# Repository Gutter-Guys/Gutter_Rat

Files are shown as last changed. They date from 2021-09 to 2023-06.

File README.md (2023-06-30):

# THIS IS A WIP USE AT YOUR OWN RISK

# Gutter_Rat
Gantry mod for the ender 6

Currently there are two options available - GR6 and GR9. 

It is recommended to look at GR9 as your first option as it is the simpliest upgrade path from a stock Ender 6. GR6 is only for those that wish to run a 6mm belt setup to possibly use the VZBot style of EVA tool heads. Definitely for those more experienced in modifying or customising printers.

The GR9 version is designed to be built with as much of the stock system as possible. Belts, Pulleys, Spacers, Motherboard and Steppers can all be reused or upgraded if you wish. This flexibilty makes this a cheap upgrade to gain access to the brilliant EVA tool head system. 

## Please join us at our Discord server for updates and assistance with the installation!
[Click Me](https://discord.gg/Wgcgkdk7qW)

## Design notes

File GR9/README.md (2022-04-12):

# Gutter_Rat 9mm Variant

This is the original modification. This mod is designed around 9mm belts with toothed GT2 pulleys and new steppers for X/Y, plus a new control board, however is designed to be the least destructive of the modifications and utilise as much of the E6 parts as possible. You will need to cut the X 2020 extrusion, but it will retain the stock mounting points in case you wish to roll back.

Currently it can be built to reuse the stock belts, stock pulleys and mounting gear, stock controller and stock motors. 

Of course, you can upgrade all these parts to better quality components, as the mod can be reconfigured easily. Please note the dimensions on the stock pulleys and spacers may vary from 3rd party options and require some further modification.

**Currently the there is a design limitation when using the stock pulleys. The stock pulleys are ~2mm wider than a standard 20t pulley. This adds 2mm to the space between the two belts, leaving a Z deflection of 2mm from front to back on the belt path. I have been running this for nearly 500hrs with no visible issues, however I can't promise this will be the case for everyone, so if possible, please look at the cheap upgrade to 20t pulleys.**

# Table of Contents
- **Before You Start**
    - [**Important Checks**](#-important-checks)
    - [Required Equipment](#required-equipment)
- **Printing Parts**
    - [Print Settings](#print_settings)
    - [Materials](#materials)
- **Assembly**
    - [Printhead](#printhead)
    - [Idlers](#idlers)
    - [Gantry Mounts](#gantry_mounts)
    - [Motor Mounts](#motor_mounts)
    - [Rails](#Rails)
    - [Other Components](#other_components)
    - [Final Assembly](#final_assembly)
- **Tuning**
    - [Klipper](#klipper)
    - [Tuning](#tuning)

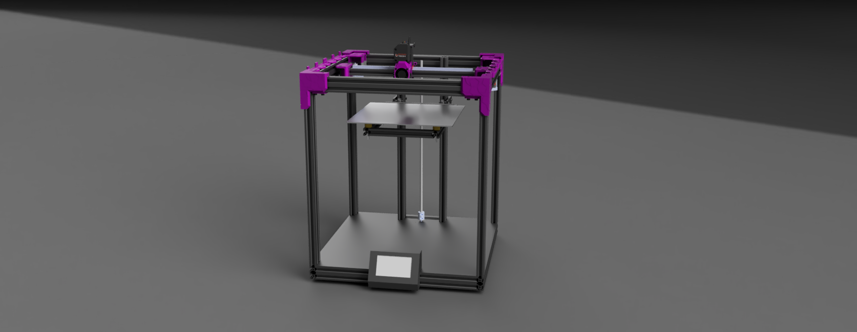
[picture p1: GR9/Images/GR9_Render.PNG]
GR9


# Before You Start

## Important Checks
**This section may sound a little intimidating, but please take the time to read it before you do anything, including ordering parts.**

The most important thing to understand is that this is a significant change to your printer. I have made the upgrade as simple as possible and attempted to avoid any permanment changes to the printer in case you wish to roll back. You will need to be comfortable with wiring, basic mechanical principles and a fairly good understanding of Klipper and printer configurations. Any damage incurred to your printer is on you - you have beeen warned.

The second most important point is to understand that this is a modification. Depending on so many things, your results may vary. Different motors, belts, pulleys, hotends etc. will result in different outcomes. Maybe faster, maybe slower, maybe better, maybe worse, it will depend on what you do and how you do it. 

Lastly, please do not attempt this if it is your only printer. I have built this upgrade twice now and both times managed to either forget to print a part or break one. If I only had the E6 I would have been stopped completely. I can also recommend printing all parts in duplicate just in case but this is personal preference. 

## Required Equipment
**This list is not complete and does not include all fixing hardware yet**

To complete this upgrade you will need the following

### GR9 STOCK
- Order:
    - 2x MGN9H 350mm rails for Y gantry (MGN12 will not fit inside the panels)
    - 1x MGN12H 350mm rail for X gantry (EVA now only supports MGN12)
    - Rasberry Pi 3B+/4/Zero2 (I am runnig a Zero 2 Wireless with PA/IS and Accelerometer)
    - 1mm washers/spacers
    - Extruder of Choice (Please use a EVA2.4 supported extruder)
    - Hotend of Choice (Please use a EVA2.4 supported hotend)
    - M3 Heat Sets (4 needed for mounting, more maybe needed for your EVA)
- Reuse
    - Stock Belts (No cutting required)
    - Stock Motors  (Some testing required)
    - Stock controller board (Please note the Klipper Configs will need to be tweaked to work on a stock board)
    - Stock pulleys
    - X Extrusion (Cut down slightly to fit, 400mm mininum, 420mm maximum) *note: you can buy and cut a new one*

### GR9 Modified (Preferred)
- Order:
    - 2x MGN9H rails for Y gantry (MGN12 will not fit inside the panels)
    - 1x MGN12H rail for X gantry (EVA now only supports MGN12)
    - Rasberry Pi 3B+/4/Zero2 (I am runnig a Zero 2 Wireless with PA/IS and Accelerometer)
    - 1mm washers/spacers
    - Extruder of Choice (Please use a EVA2.4 supported extruder)
    - Hotend of Choice (Please use a EVA2.4 supported hotend)
    - GT2 Belts
    - 2x Nema17 motors of your choice
    - Controller with at least 4x TMC2209 (Example config is with SKR E3 v2), 7x TMC2209 required for Tri-Z modifications
    - M3 Heat Sets (4 needed for mounting, more maybe needed for your EVA)
    - 13mm wide 20t idlers (6 toothed and 2 smooth)
- Reuse
    - X Extrusion (Cut down slightly to fit, 400mm mininum, 420mm maximum) *note: you can buy and cut a new one*

### Can I fit MGN12H on my Y if I already have them?
Short answer: Yes it can be made to work

Longer answer: You can use the GR9_MGN12_Gantry_Mount_TEST file for fitting the X gantry to the E6 via MGN12H rails. The issue is the over hang of the carriage is 2-3mm each side, which conflicts with the stock side panels. If you choose this change, you will need to *very* carefully space out the side panels. A couple check washers will work, or print a small spacer. Just be **very careful as this will add tension to the panels and may crack the acrylic if not tensioned properly!!!** Please, please be aware of this and take care. I would suggest adding spacers of varying depth down the side to avoid a shape bend on the last part of the panel. 

MGN12H Spacer

# Printing Parts

## Print Settings
Not going to lie, the best parts settings I have worked with yet are the Voron settings. Its a good base to start from, but please feel free to tune in what works for you:
- Layer height: 0.2mm
- Extrusion width: 0.4mm
- Infill percentage: 40%
- Infill type: Gyroid
- Wall/Perimeters: 4
- Top/Bottom layers: 5
- Supports: Brim only if required

## Materials
I have succesfully printed this upgrade in both PETG and ABS.

### PETG
PETG is a crazy material, and the layer adhesion is amazing. For this reason it is quite a good option for printing the parts for this modification. I would strongly suggest the wider fan duct option thouoh, as mine did sag a little over time. If you plan to enclose the printer long term, then PETG can be used for a short period. At chamber temps over 50c the PETG *will sag* and can cause problems, but it might be enough to get a reprint in ABS.

### ABS
I love and hate ABS. 99% of my prints are in ABS and my printer is fully enclosed, so ABS parts were a must. The parts are fine with a little bit of shrinkage so no scaling is required, however some screw holes may need to be cleared with a drill bit. The EVA parts are usually supplied from RatRig in PETG but I have had no issues with them printed in ABS. Just be aware that ABS can delamiinate easily, so be careful with the trapped nuts in the EVA parts.

### PLA
Don't bother. It won't work and aside from some of the cosemtic parts, it just isn't worth the hassle or risk.

### Other Materials
No idea. Could work, might not. Let me know if you try something and it works, I will update the notes. 

### Colours 
Up to you, but I have marked each part as A (Accent) or B (Base) so you can do a two tone look. Otherwise go crazy :)

# Assembly

## X Extrusion
If you are using the stock X extrusion, it will need to be shortened before it can be used. This can be done by cutting it down to between 400mm to 420mm. We designed the Gantry Brackets to not need an exact measurement, however if you remove a little bit from each end to get to 400mm, you can avoid the original E6 mounting holes allowing the X extrusion to used if you roll back to stock later on. Or simply use a fresh extrusion, completely your choice. 

X 2020

## Rails
Please refer to online guides for mounting and and cleaning rails. MGN9 for Y and MGN12 for X. Nothing special needed, just center them as best you can. It is easier to mount the Y rails after you have mounted the Motor Mounts. Mounting guides are included in the STL folder to make alignment easier. (Each rail need 7 M3x8mm and 7 M3 drop/t nuts)

## Printhead
The EVA printhead system is amazingly well designed and very flexible. It was the sole reason this upgrade was completed. For the moment, this is compatible with EVA 2.4 setups so go crazy. If it fits EVA, it will fit this setup. I will not be duplicating any of their work here, please go directly to the EVA website and get all you need from there, including BOM and print configurations. 

Mouint it to the X rail now as it can be pain to add later when the rail is in the printer, but do not add the Hotend as you will need access to the belt mounts.

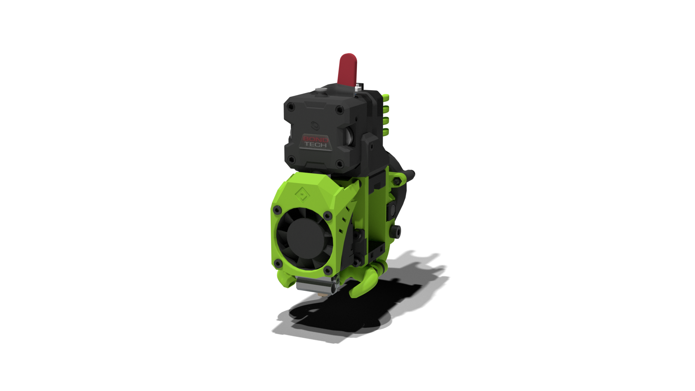
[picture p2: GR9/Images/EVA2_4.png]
EVA2.4


## Idlers
The idler setup is very simple and easy to put together.

### Stock Pulleys
The two vertical M5x10mm screws will need to insert first as they can be hard to get in once the pulleys are in place.

From the top, you will need:
- 5mm printed spacer
- Pulley
- Compression washer (reused from E6)
- Pulley

Stock Idler Config

Then, simply reuse the long screw from the E6 to fix it together, with a washer on the bottom below the nut. It may seem a little loose in the idler, so tighten until it no longer wobbles, then apply loctite (or clear nail polish) to the remaining thread to hold the nut in place.

Repeat for the other side. Then mount with M5x10mm screws and M5 drop nuts.

### After market pulleys
The two vertical M5x10mm screws will need to insert first as they can be hard to get in once the pulleys are in place.

The current configuration has been tested successfully with standard 20t ilders. You will need a 5mm bore, 13mm width idler. Anything more than 13mm width will require you to adjust the spacer configuration. 

From the top you will need:
- 6mm printed spacer
- Pulley
- 1mm spacer
- Pulley

20t Idler Config

## Gantry
A little more complicated than the idlers, but simple enough. 

First, mount the Gantry Mounts to the Y Rail carriages. This is straight forward, and makes the final assembly easier. This will need 4 M3x6mm per side.

Then, add the two heat sets to each Gantry Bracket. Again, fairly straight forward. Preferred are M3x5x4mm heat sets, a total of 4 will be needed. 

Now the complicated part. Align the Gantry Mounts in front of you so they sit as they would in printer. You will notice that one side of the Mounts has a slot and the other side is inclosed. They are set up as follows: (refer to pictures to confirm)

### Stock Pulleys

#### Left - Slotted side
From the top you will need:
- 2mm Printed Spacer
- Stock pulley
- 13mm Printed Spacer

#### Left - Enclosed side
From the top you will need:
- 15mm Printed Spacer
- Stock pulley
- 1mm washer/shim

Gantry Stock Pulley Config Left Side

#### Right - Slotted side
From the top you will need:
- 15mm Printed Spacer
- Stock pulley
- 1mm washer/shim

#### Right - Enclosed side
From the top you will need:
- 2mm Printed Spacer
- Stock pulley
- 13mm Printed Spacer

Gantry Stock Pulley Config Right Side

Then, simply reuse the long screw from the E6 to fix it together, with a washer on the bottom below the nut. It may seem a little loose in the idler, so tighten until it no longer wobbles, then apply loctite (or clear nail polish) to the remaining thread to hold the nut in place.

### After market pulleys
The current configuration has been tested successfully with standard 20t ilders. You will need a 5mm bore, 13mm width idler. Anything more than 13mm width will require you to adjust the spacer configuration. 

#### Left - Slotted side
From the top you will need:
- 3mm Printed Spacer
- Pulley
- 14mm Printed Spacer

#### Left - Enclosed side
From the top you will need:
- 16mm Printed Spacer
- Pulley
- 1mm washer/shim

Gantry 20t Pulley Config Left Side

#### Right - Slotted side
From the top you will need:
From the top you will need:
- 16mm Printed Spacer
- Pulley
- 1mm washer/shim

#### Right - Enclosed side
- 3mm Printed Spacer
- Pulley
- 14mm Printed Spacer

Gantry 20t Pulley Config Right Side

Then, simply use  M5x45mm bolts to fix it together, with a washer on the bottom below the nut. Then apply loctite (or clear nail polish) to the remaining thread to hold the nut in place.

## Motor Mounts
The motor mount comes in two peices. Mount the stepper to the  base with 4 M3x8mm bolts, then attach firmly to the frame with M5's. Make sure the motor orientation is such that th cables face towards the  back for easy access.

Then, make sure the motor pulleys are orientated correctly. The left pullet will be as per the picture, with the pulley a fraction above flush with the top of the stepper. The right one will be inverted and 10mm from the stepper motor. 

It is easier to run the belts now, before you add the top half - trust me it will be so much easier. Come back to the next bit once they are done. 

Finally, attach the top half and fix to the frame with M5's. Once attached, use the 2 M3x40mms per side to anchor the two halves to the stepper motor. 

Motor Mount

## Other Components
Similar to the rails, I will leave to you and the internet to work out how to mount things like custom controllers, Raspberry Pi etc. I only suggest to keep it simple and don't take too much on at one time as it will make trouble shooting hard.

## Final Assembly
Now for the fun part - putting it all together.

### Mounting Hardware
At this point, you should have the motors mounted, the ilders completed and mounted, Gantry Brackets completed, EVA and only the Gantry Mounts in place on the Y rails. If not, go back and finish these steps first.

First, add the two Gantry Brackets to the X extrusion. They should slip on and be firm but able to be moved without to much effort. You will need to adjust these later on, so its important they can move. Add the two M5x6mm screws and drop/t nuts per side now but do not over tighten yet. 

Now, position the X extrusion in the printer so that it sits on the two Gantry Mounts attached to the Y rails. Use M3 screws to attach to the Gantry Mounts. You should now have the X extrusion mounted and it should slide easily on the Y rails. If not, adjust the Gantry Brackets on the X extrusion until it does move easily. **DO NOT FORCE IT!**

**Once the X is moving freely, we need to de-rack the gantry. This is super, super important. For reference, Nero3DP has a great video on YouTube that I highly recommend you watch as an explanation, even though it references a Voron 2.4 printer.**

To de-rack the E6, slide the X all the way to the front of the printer. Both Gantry Brackets should be touching the idlers evenly. Typically, one will be touching and one won't. This twist is what we need to remove. Gently, while all mounting screws are loose, fiddle with the various mounts until both Gantry brackets are hard up against the Idlers. Now go back over *every* screw and tighten them in place. Check the X is still square to the two idlers and slide it back and forth all the way to the Motor Mounts to ensure there is no binding. 

Once De-racked, it is time to add the belts. This is my way of mounting them, but you are welcome to do it however it works for you. Add one end of each belt to the tensiner blocks on the EVA printhead, making sure the belts are fully in the blocks. Insert them into the printhead and tighten until they are both even with the back of the EVA printhead. **Take the time to make sure they are even at this point**

Now route the belts through the printer and back to the print head. Put the end of each belt on printhead so that 1-2 ridges extend past the belt grabbers. **Make both sides the same**.

The belt should be fairly loose if you have used the stock belts. If you bought new belts, over hang as much as needed, but keep the lengths the same. Slowly tighten the belt tensioner screws until the belts are the correct tension. Again, you need to Google this as there are dozens of suggested methods floating around out there and everyone has a recommended tension.

If the belts are done, make sure the XY motors are disconnected and move the X back and forth, checkin the racking at the same time. If the X has misaligned again, change the belt tension until it is de-racked again. 

After this is dine, you can mount your Hotend to the Printhead and congrats!

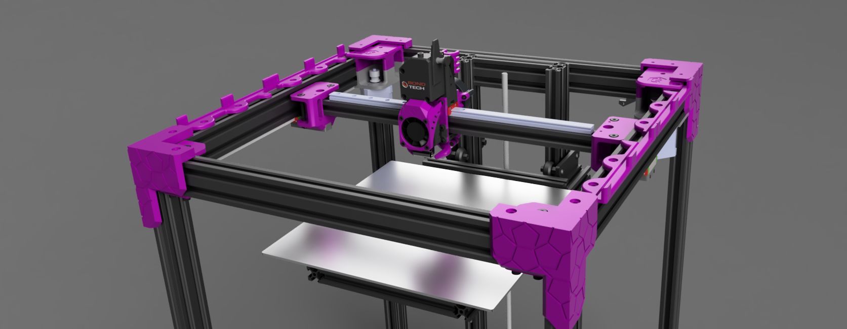
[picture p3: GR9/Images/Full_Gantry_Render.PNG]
Completed Gantry


# Tuning

## Klipper
Klipper is both amazing and magical to most. I do not claim to be any good with Klipper, however I have attached a sample config if you wish to look over it. You will need to adjust the pin IDs for your controller, as well as sensorless homing if you went that way. Otherwise, ask questions on Discord and we will help where we can.

## Tuning
There are many wasy to skin a cat, and many ways to tune a printer. What I do recommend is to start with Superslicer. Its well supported and better yet, it allows you to use what I think is the best tuning guide you there - Andrew Ellis Print Tuning Guide. It is written for a Voron, but it is the most detailed and simple guide out there. 

I have attached a copy of the SuperSlicer profile I use, which was based on the above guide. With 1.8 motors and Sherpa Mini, I can sit comfortably at the following print settings;

150mm/s outer walls at 5k acc
250mm/s inner at 9k acc
300mm/s infill at 12k acc
120mm/s top infill/surface at 5k acc
ABS with 80% cooling fixed speed
10% infill retic
Mono surface

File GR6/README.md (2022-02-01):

# !!! This version is untested and very very much a Beta - Use at your own risk !!

# Gutter_Rat 6mm Variant
This version of the Gutter Rat modification is the least tested.

This variation was designed with the VZBot hotend in mind with a MGN9 X rail but has since been changed back to MGN12 as per normal EVA, but has no other improvements over the 9mm (GR9)version. You will need to run a custom EVA faceplate as well. This mod is designed around 6mm belts with toothed GT2 pulleys and new steppers for X/Y, plus a new control board. This mod will require a new X 2020 extrusion or a destructive change to the stock X 2020 shortening.

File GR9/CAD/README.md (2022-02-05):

# Gutter_Rat 9mm Variant

A short disclaimer on the STEP file.

This is a full assembly of all parts per current STL files. Take note of the following:

- No motors are currently mounted until we decide on a preferred option. Not that they make much difference, this will follow soon.

- The EVA printhead in the Assembly is only for visual representation and not to be used for generating STLs. It is *NOT* the current version available on the EVA website. Please do not use it other than to give you an idea on mounting and orientation

- The pulleys are not added to the various Ilder and Gantry brackets, again because they are a variable part. They are in the STEP file but hidden, so you can show them and play around with your own configuration if you so wish, other wise follow the assembly guide or ask on Discord. 

- There is a Canopy mount in the STEP file, design to hold the stock canopy in place. It is a WIP component and only tested on a single printer. Call it a Beta if you wish, it needs to be refined slightly. You are welcome to use and test it and feedback would be appreciated.

Otherwise, Enjoy!

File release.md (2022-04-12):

# Beta 0.4.0

Quite a few updates:

Added MGN12H Y carriage support (resolves #20 )
Fixed Gantry Bracket to remove poorly designed fillets and remove legacy defects that have occurred over the various versions
Remove incorrect fillet on Idler Mount (Fixes #26 )
Address belt pathing issues with stock belts and idlers by removing the built in spacers on the Gantry Bracket (fixes #25 )
Add printable spacers based on 13mm 20t idlers and stock 14mm idlers
Updated documentation to clarify idler and spacer configurations
Fixed multiple typos in documentation (resolves #24 )
Added photos to Readme
Updated CAD which displays full frame for future project work

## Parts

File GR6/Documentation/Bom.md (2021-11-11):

| Item | Quantity | Price | Link |
|-- | -- | --- | ---  |
| | | | |

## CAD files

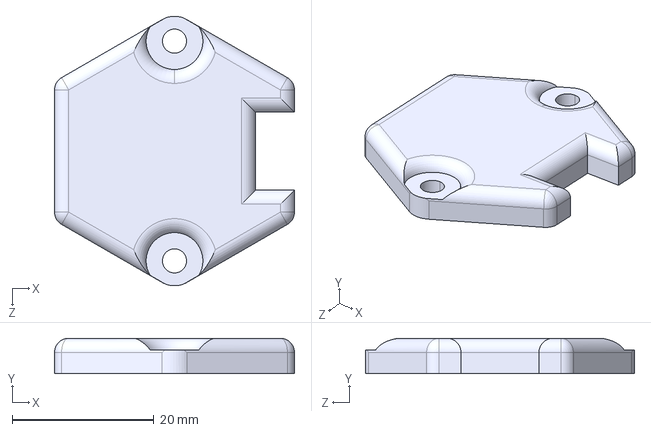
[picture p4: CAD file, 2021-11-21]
GR6/CAD/Gantry_Mount_Rail_Bracket[L]_{b}.STEP
33.8 x 5.00 x 38.0 mm

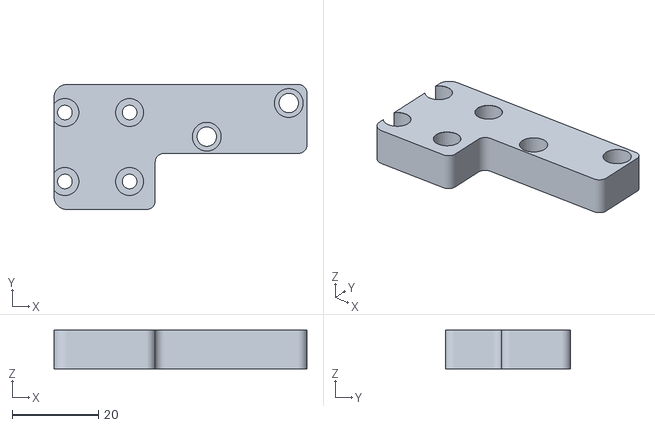
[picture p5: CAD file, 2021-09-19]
GR6/STLs/Gantry_Mount_Bracket_[L]_{b}.STL
58.7 x 29.0 x 9.00

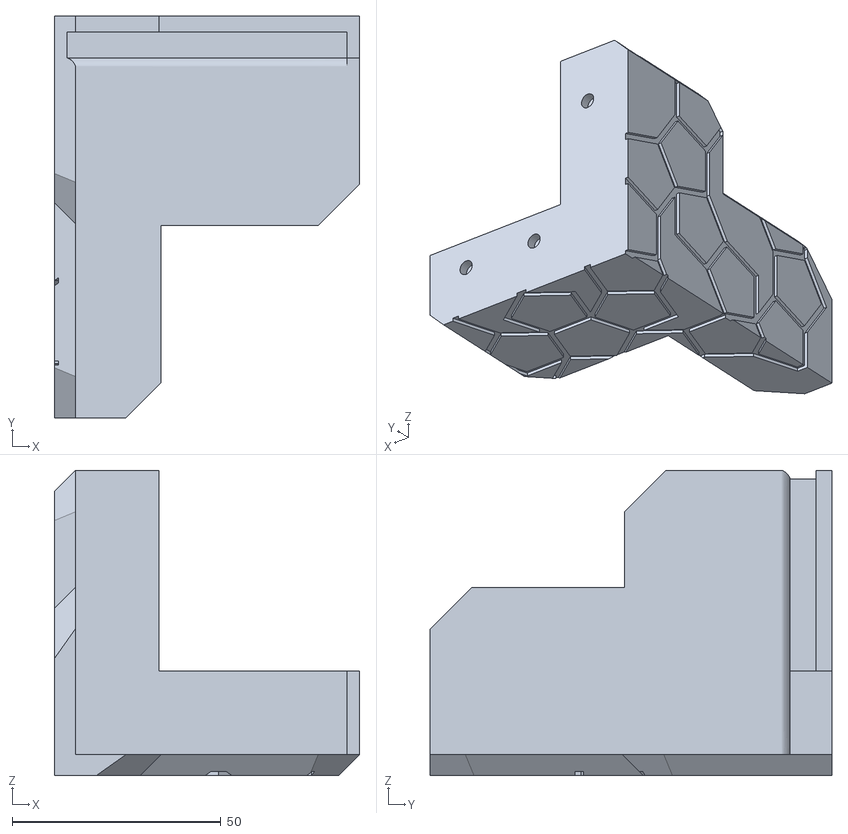
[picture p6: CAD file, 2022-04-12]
GR9/STLs/GR9_Canopy_Mount [RearLeft] {a}.stl
73.0 x 96.1 x 73.0

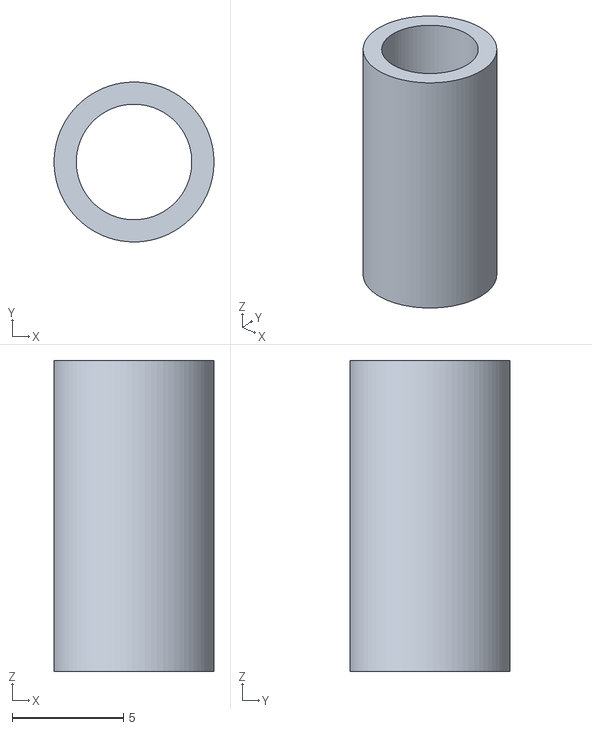
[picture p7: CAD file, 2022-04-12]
GR9/STLs/Spacers/20t Pulley/14mm Spacer.stl
7.20 x 7.20 x 14.0

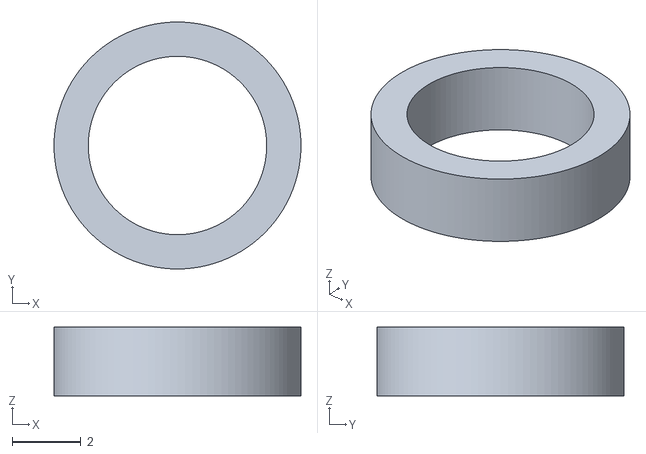
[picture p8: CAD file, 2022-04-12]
GR9/STLs/Spacers/Stock Pulley/2mm Spacer.stl
7.20 x 7.20 x 2.00

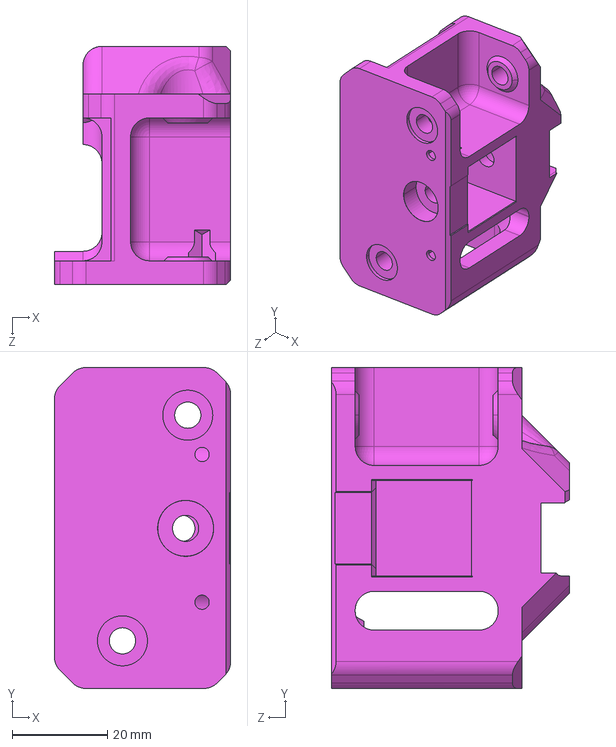
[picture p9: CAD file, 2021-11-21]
GR6/CAD/Gantry_Mount_[L]_{b}_20t.STEP
37.0 x 67.3 x 50.0 mm

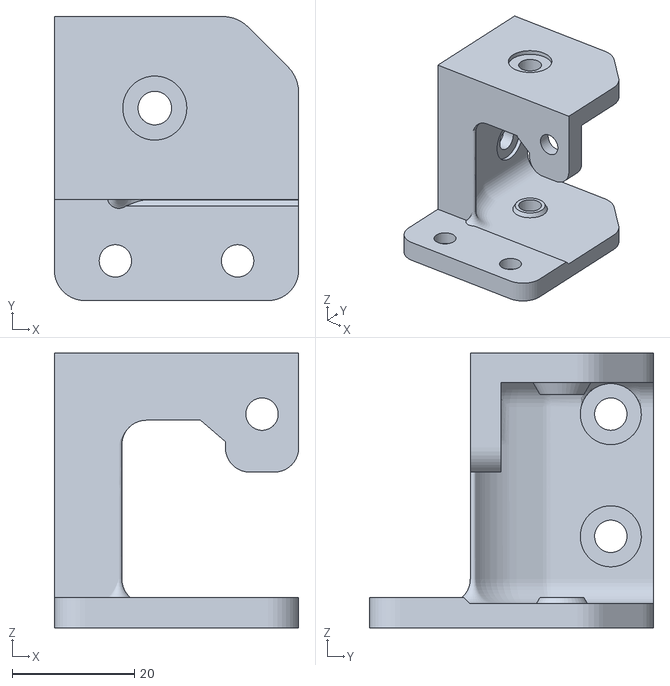
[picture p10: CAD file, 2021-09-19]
GR6/STLs/Idler_Mount_[L]_{a}.STL
40.0 x 46.5 x 45.0

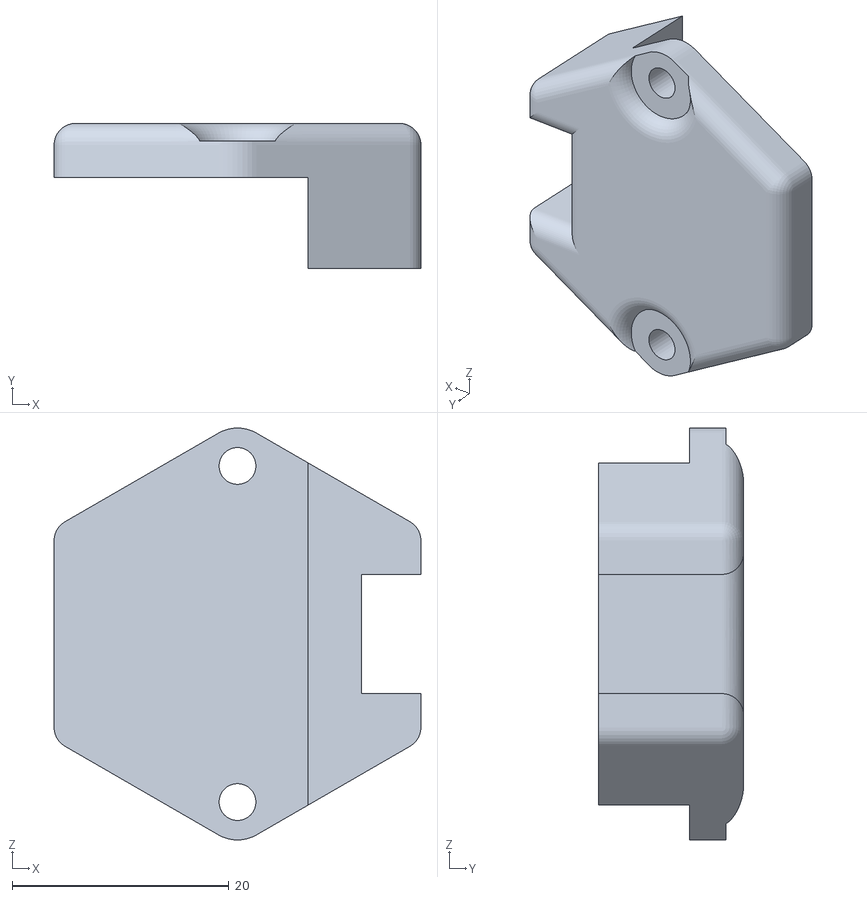
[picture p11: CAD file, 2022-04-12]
GR9/STLs/GR9_Gantry_BumpStop [Left] {b}.stl
33.8 x 13.4 x 38.0

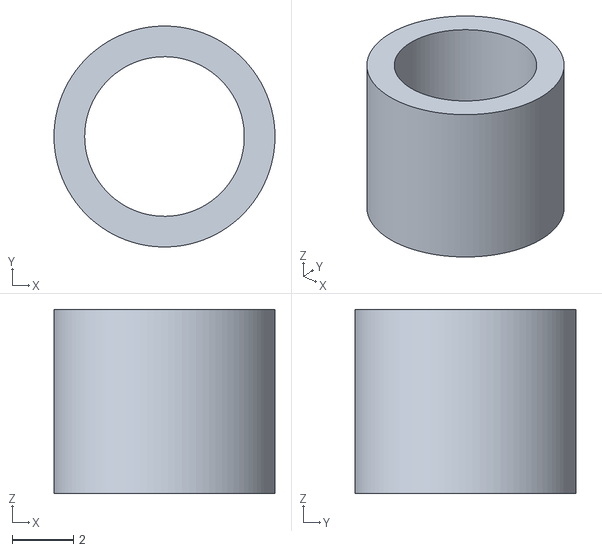
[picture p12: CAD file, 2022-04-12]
GR9/STLs/Spacers/20t Pulley/6mm Spacer.stl
7.20 x 7.20 x 6.00

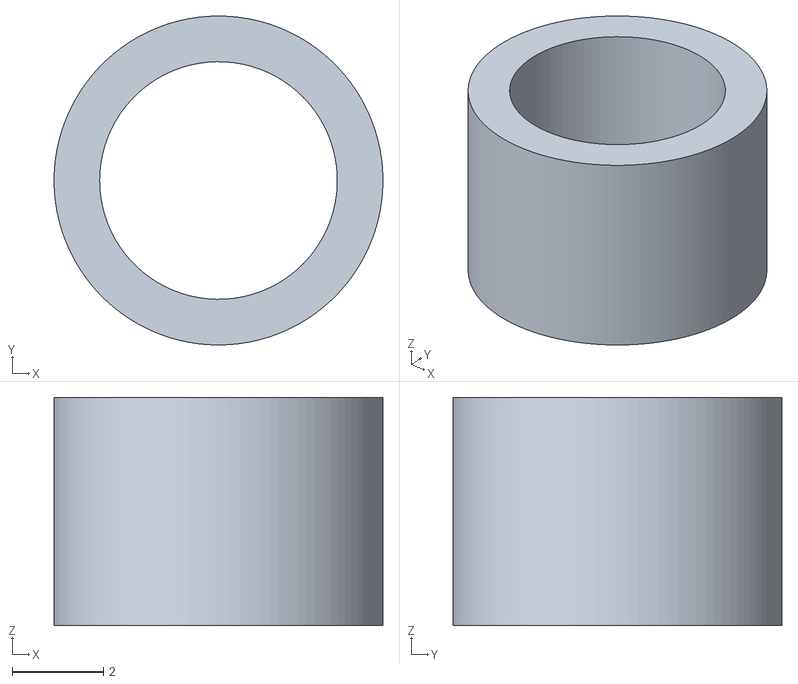
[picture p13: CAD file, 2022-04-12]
GR9/STLs/Spacers/Stock Pulley/5mm Spacer.stl
7.20 x 7.20 x 5.00

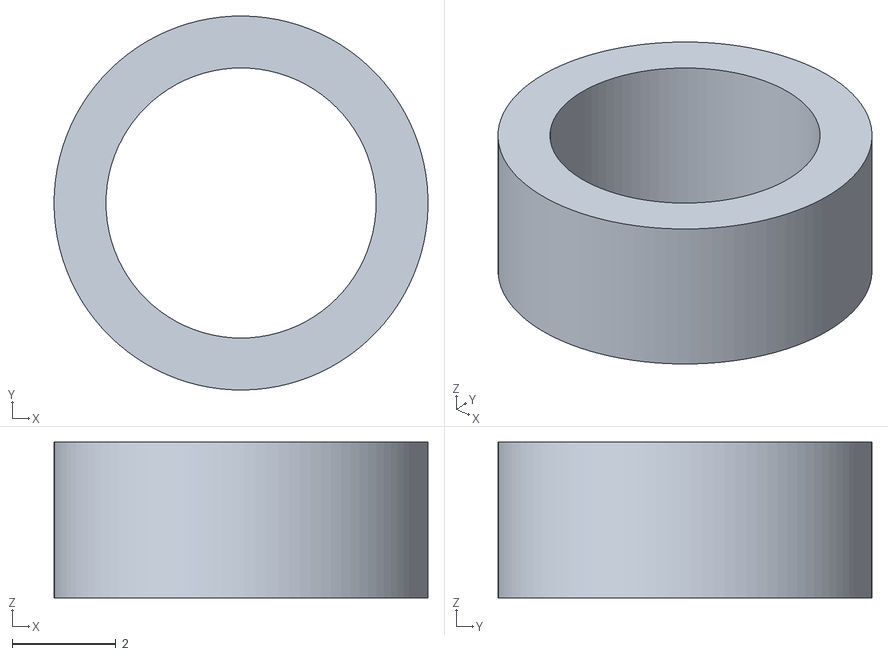
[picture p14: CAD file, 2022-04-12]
GR9/STLs/Spacers/20t Pulley/3mm Spacer.stl
7.20 x 7.20 x 3.00

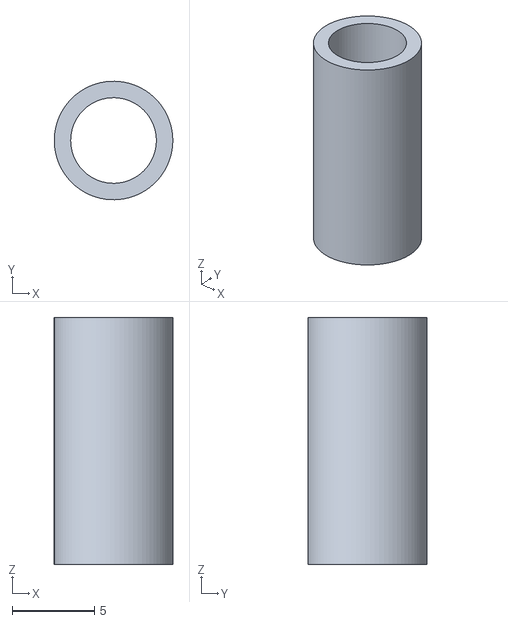
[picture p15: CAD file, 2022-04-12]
GR9/STLs/Spacers/Stock Pulley/15mm Spacer.stl
7.20 x 7.20 x 15.0

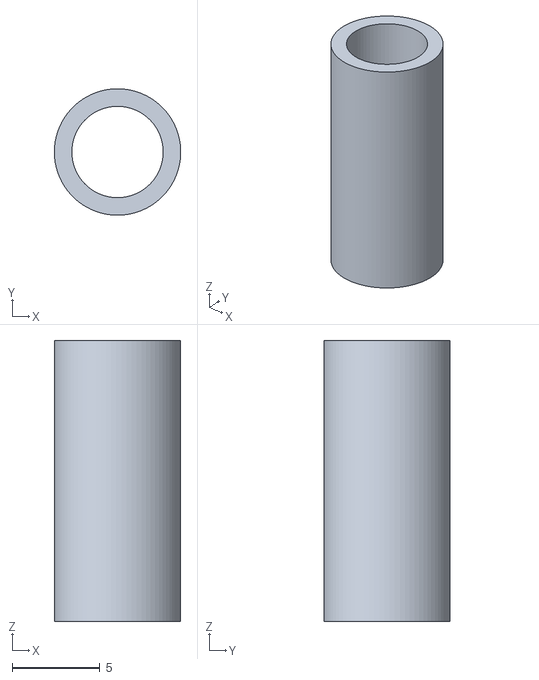
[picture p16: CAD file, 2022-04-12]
GR9/STLs/Spacers/20t Pulley/16mm Spacer.stl
7.20 x 7.20 x 16.0

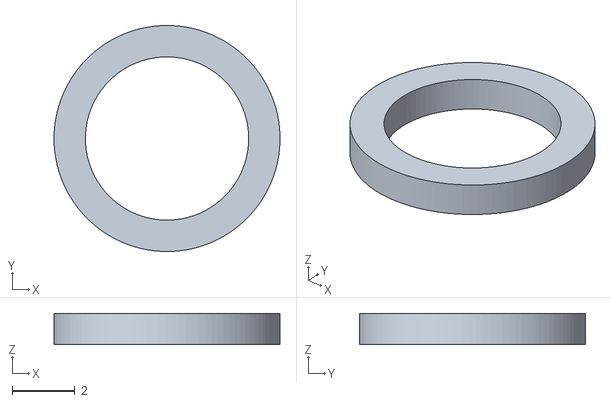
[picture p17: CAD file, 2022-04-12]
GR9/STLs/Spacers/Stock Pulley/1mm Spacer.stl
7.20 x 7.20 x 1.00

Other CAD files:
GR6/STLs/Gantry_Mount_[L]_{a}.STL
GR9/STLs/GR9_Gantry_Bracket [Right] {a} v1 .stl
GR6/STLs/Gantry_Mount_[R]_{a}.STL
GR9/STLs/GR9_Gantry_Bracket [Left] {a} v1 .stl
GR6/STLs/Gantry_Mount_Rail_Bracket[L]_{b}.STL
GR6/STLs/Gantry_Mount_[L]_{b}_20t.STL
GR6/STLs/Idler_Mount_[R]_{a}.STL
GR9/STLs/GR9_Canopy_Mount [FrontLeft] {a}.stl
GR9/STLs/GR9_Canopy_Support [Side] {a}.stl
GR9/STLs/GR9_Frame_Brace [TEST] {a}.stl
GR9/STLs/GR9_Gantry_Mount [Left] {b}.stl
GR9/STLs/GR9_Gantry_Mount [Right] {b}.stl
GR9/STLs/GR9_Gantry_Mount_MGN12 [TEST] {b}.STEP
GR9/STLs/GR9_Idler [Left] {a} v1.stl
GR9/STLs/GR9_Idler [Right] {a} v1.stl
GR9/STLs/GR9_MGN12_guide_block_2020.stl
GR9/STLs/GR9_MGN9_guide_block_2020.stl
GR9/STLs/GR9_MotorMount_Bottom [Left] {b}.stl
GR9/STLs/GR9_MotorMount_Bottom [Right] {b}.stl
GR9/STLs/GR9_MotorMount_Top [Left] {a}.stl
GR9/STLs/GR9_MotorMount_Top [Right] {a}.stl
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

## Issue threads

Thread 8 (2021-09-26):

Add Y position end stop to Pulley Idler

ViralEntity, 2021-09-26:
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

Add a standoff to allow Y end stop via homeless sensor to Idler pulley.
Add M2 holes to allow mounting of a microswitch

@Johnnymakesthings to confirm the dimensions and allow maximum bed use.

_Note:_ Needs to be orientated to avoid having to support this print as it is currently an unsupported part

Closed 2022-02-02.

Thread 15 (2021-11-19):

Increase tolerances on Gantry mount

ViralEntity, 2021-11-19:
Tolerances on x 2020 can be increased slight as we use fittings to secure it. Should also fillet edge to help guide it in

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

Closed 2022-02-01.

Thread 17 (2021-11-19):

Rail bracket need improving/redesign

ViralEntity, 2021-11-19:
Not happy with the Gantry_Mount_RailBracket[L]{b}. It needs a better design to allow for easier printing and no supports

Closed 2022-02-01.

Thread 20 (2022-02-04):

Add support for MGN12 rails on Y

ViralEntity, 2022-02-04:
This will also need to mention the use of spacers for side panels, maybe make them a printed item too

Closed 2022-04-12.

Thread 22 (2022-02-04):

Frame supports needed

ViralEntity, 2022-02-04:
The frame needs stiffening at higher accelerations. Corner braces should be a simple printed fix.

Jubidition, 2022-02-04:
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

ViralEntity, 2022-02-05:
Perfect, flick me the STL and I will add it for now and update the CAD later.

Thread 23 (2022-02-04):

MGN Rail sizes

Renidd, 2022-02-04:
current required equipment states.
2x MGN9 rails for Y gantry (MGN12 will not fit inside the panels)
Should read
2x MGN9 (350mm) rails for Y gantry (MGN12 will not fit inside the panels)

and
1x MGN12 rail for X gantry (EVA now only supports MGN12)
should read
1x MGN12 (350mm) rail for X gantry (EVA now only supports MGN12)

ViralEntity, 2022-02-04:
Great point, will fix today

Closed 2022-02-05.

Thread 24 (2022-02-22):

misstype

Niken02, 2022-02-22:
In gantry section there is 3 left sides and 1 right side in the stock pulley section

ViralEntity, 2022-02-26:
Thanks, has been addressed and will close this shortly

Closed 2022-04-12.

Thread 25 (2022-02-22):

Idler spacers

Niken02, 2022-02-22:
Cant find the stls for the 7 and 5 mm spacers called for in the idler section.

Johnnymakesthings, 2022-02-25:
for the 9mm or 6mm

Niken02, 2022-02-26:
For the GR9

ViralEntity, 2022-02-26:
Thanks, these have been made are being uploaded now. I have matched the spacers to the readme as well.

Closed 2022-04-12.

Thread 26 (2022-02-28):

[Issue]: front idlers have defect

Renidd, 2022-02-28:
### Contact Details

_No response_

### What happened?

the front left and right idlers have a slope that gets in the way of mounting.
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

### Version

present in all ver's on gethub

### Which variant are you using?

GR9

### Relevant log output

_No response_

### Code of Conduct

- [X] I agree to follow this project's Code of Conduct

Renidd, 2022-02-28:
Attached

Renidd, 2022-02-28:
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

Renidd, 2022-02-28:
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

Renidd, 2022-02-28:
but this is the slope im talking about.. not the one under the idler's
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

ViralEntity, 2022-02-28:
Gotcha. Thanks easy fix will remove fillet

ViralEntity, 2022-03-01:
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

Closed 2022-04-12.

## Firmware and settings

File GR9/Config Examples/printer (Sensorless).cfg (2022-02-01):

################################################################################
# ~~~~~~~~~~~~~~~~~~~~~~~~  PRINTER CONFIGURATION   ~~~~~~~~~~~~~~~~~~~~~~~~~~ #
################################################################################

################################################################################
# Configuration File Links #
################################################################################
[include kiauh_macros.cfg]
[include GCODE_Macros.cfg]
[include GPIO_Macros.cfg]

################################################################################
# MCU Definitions #
################################################################################
[mcu]
serial: /dev/serial/by-id/usb-Klipper_lpc1769_1AD0FF15C19869AF38CC425EC32000F5-if00

[mcu rpi]
serial: /tmp/klipper_host_mcu

################################################################################
# Required Configuration #
################################################################################

[pause_resume]

[respond]

[display_status]

[virtual_sdcard]
path: ~/gcode_files

[static_digital_output tmc_standby_pins]
pins: !P3.26, !P3.25, !P1.18, !P1.19, !P2.13

[board_pins]
aliases:
    # EXP1 header
    EXP1_1=P2.8,  EXP1_3=P0.19, EXP1_5=P0.20, EXP1_7=P0.17, EXP1_9=<GND>,
    EXP1_2=P0.16, EXP1_4=<RST>, EXP1_6=P0.15, EXP1_8=P0.18, EXP1_10=<5V>

################################################################################
# Kinematics #
################################################################################
[printer]
kinematics: corexy
max_velocity: 300
max_accel: 1000
max_z_velocity: 5
max_z_accel: 100

[stepper_x]
#step_pin: P1.4
#dir_pin: !P1.8
#enable_pin: !P1.0
step_pin: P2.11
dir_pin: !P2.12
enable_pin: !P0.21
microsteps: 16
rotation_distance: 40
#endstop_pin: ^P1.29 #For physical endstop
position_endstop: 0
position_max: 285
homing_speed: 50
homing_retract_dist: 0
endstop_pin: tmc2209_stepper_x:virtual_endstop #For sensorless homing

[tmc2209 stepper_x]
#uart_pin: P1.1
#diag_pin: P1.29
uart_pin: P0.22
diag_pin: P1.25
driver_SGTHRS: 135
run_current: 0.800
hold_current: 0.700
stealthchop_threshold: 0

[stepper_y]
step_pin: P1.14
dir_pin: !P1.15
enable_pin: !P1.9
microsteps: 16
rotation_distance: 40
#endstop_pin: ^P1.28 #For physical endstop
position_endstop: 0
position_max: 260
homing_speed: 50
homing_retract_dist: 0
endstop_pin: tmc2209_stepper_y:virtual_endstop #For sensorless homing

[tmc2209 stepper_y]
uart_pin: P1.10
diag_pin: P1.28
driver_SGTHRS: 135
run_current: 0.800
hold_current: 0.700
stealthchop_threshold: 0

[stepper_z]
step_pin: P4.29
dir_pin: !P4.28
enable_pin: !P1.16
microsteps: 16
rotation_distance: 8
#endstop_pin: ^P1.27
#position_endstop: 0.0
endstop_pin: probe:z_virtual_endstop
position_max: 385
position_min: -3

[tmc2209 stepper_z]
uart_pin: P1.17
#diag_pin: P1.27
run_current: 0.800
hold_current: 0.700
stealthchop_threshold: 0

################################################################################
# BLTouch #
################################################################################
[bltouch]
sensor_pin: ^P1.22
control_pin: P1.23
x_offset: 28
y_offset: 13
#z_offset: 1
speed: 3.0

#[safe_z_home]
#home_xy_position: 115,115 
#speed: 50
#z_hop: 10              
#z_hop_speed: 5

[bed_mesh]                      
speed: 120
mesh_min: 43, 18
mesh_max: 257, 247
algorithm: bicubic
probe_count:5,5

[homing_override]
axes: xyz
set_position_z: 0
gcode:
  G1 Z10 F600
  SENSORLESS_HOME_X
  SENSORLESS_HOME_Y
  G1 X115 Y115 F9000
  G28 Z
      
[screws_tilt_adjust]
screw1: 220,220
screw1_name: front left screw
screw2: 30,220
screw2_name: front right screw
screw3: 30,30
screw3_name: rear right screw
screw4: 220,30
screw4_name: rear left screw
horizontal_move_z: 10.
speed: 50.
screw_thread: CW-M3      

################################################################################
# Extruder #
################################################################################
[extruder]
step_pin: !P2.6
dir_pin: P2.7
enable_pin: !P0.4
microsteps: 16
rotation_distance: 22.67895
full_steps_per_rotation: 200
gear_ratio: 50:10
max_extrude_only_distance: 1400.0
max_extrude_only_velocity:  75.0
max_extrude_only_accel: 1500
nozzle_diameter: 0.400
filament_diameter: 1.750
heater_pin: P2.3
sensor_type: NTC 100K beta 3950
sensor_pin: P0.24
#control: pid
#pid_Kp: 21.527
#pid_Ki: 1.063
#pid_Kd: 108.982
min_temp: 0
max_temp: 280

[tmc2209 extruder]
uart_pin: P0.5
#diag_pin: P1.26
interpolate: True
run_current: 0.30
hold_current: 0.35
stealthchop_threshold: 0

#[extruder1]
#step_pin: P2.11
#dir_pin: P2.12
#enable_pin: !P0.21
#heater_pin: P2.4
#sensor_pin: P0.23
#...

#[tmc2209 extruder1]
#uart_pin: P0.22
##diag_pin: P1.25
#...

################################################################################
# Heater Bed #
################################################################################
[heater_bed]
heater_pin: P2.5
sensor_type: EPCOS 100K B57560G104F
sensor_pin: P0.25
#control: pid
#pid_Kp: 54.027
#pid_Ki: 0.770
#pid_Kd: 948.182
min_temp: 0
max_temp: 130

################################################################################
# Cooling #
################################################################################
[fan]
pin: P2.1

[heater_fan nozzle_cooling_fan]
pin: P2.2

################################################################################
# Chamber # 
################################################################################
[temperature_sensor raspberry_pi]
sensor_type: temperature_host
min_temp: 10
max_temp: 100

################################################################################
# Accelerometer # 
################################################################################
[adxl345]
cs_pin: rpi:None

[resonance_tester]
accel_chip: adxl345
probe_points: 125, 125, 50

#*# <---------------------- SAVE_CONFIG ---------------------->
#*# DO NOT EDIT THIS BLOCK OR BELOW. The contents are auto-generated.
#*#
#*# [extruder]
#*# control = pid
#*# pid_kp = 22.710
#*# pid_ki = 1.294
#*# pid_kd = 99.638
#*#
#*# [heater_bed]
#*# control = pid
#*# pid_kp = 69.091
#*# pid_ki = 1.143
#*# pid_kd = 1044.144
#*#
#*# [bltouch]
#*# z_offset = 2.400
#*#
#*# [bed_mesh default]
#*# version = 1
#*# points =
#*# 	-0.177500, -0.107500, 0.010000, -0.032500, -0.052500
#*# 	-0.170000, -0.065000, -0.057500, -0.040000, -0.062500
#*# 	-0.130000, -0.020000, 0.040000, 0.067500, 0.050000
#*# 	-0.085000, 0.070000, 0.070000, 0.097500, 0.062500
#*# 	-0.142500, 0.000000, 0.072500, 0.047500, 0.057500
#*# tension = 0.2
#*# min_x = 43.0
#*# algo = bicubic
#*# y_count = 5
#*# mesh_y_pps = 2
#*# min_y = 18.0
#*# x_count = 5
#*# max_y = 247.0
#*# mesh_x_pps = 2
#*# max_x = 257.0
#*#
#*# [input_shaper]
#*# shaper_type_x = mzv
#*# shaper_freq_x = 65.4
#*# shaper_type_y = mzv
#*# shaper_freq_y = 44.4

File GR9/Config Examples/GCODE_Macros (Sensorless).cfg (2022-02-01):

################################################################################
# ~~~~~~~~~~~~~~~~~~~~~~~~       GCODE Macros       ~~~~~~~~~~~~~~~~~~~~~~~~~~ #
################################################################################

################################################################################
# General #
###############################################################################
[gcode_macro Print_Start]
gcode:
    {% set BED_TEMP = params.BED_TEMP|float %}
    {% set EXTRUDER_TEMP = params.EXTRUDER_TEMP|float %}
    G90 ; use absolute coordinates
    M83 ; extruder relative mode
    M104 S150 ; set extruder temp 150c for auto bed leveling
    M140 S{BED_TEMP} ; set bed temp
    M190 S{BED_TEMP} ; wait for bed temp
    G28 ; home all
    #BED_MESH_CALIBRATE ; auto bed levelling
    M104 S{EXTRUDER_TEMP} ; set extruder temp
    G1 Z50 F240 ; lower bed before moving
    G1 X15 Y10 F3000 ; move to start position
    M109 S{EXTRUDER_TEMP} ; wait for extruder temp
    G1 Z0.28 F240 ; lower to start position
    G92 E0 ; reset extruder
    G1 Y260 E15 F1500 ; intro line
    G1 X15.3 F5000 ; move to the side
    G92 E0 ; reset extruder
    G1 Y10 E15 F1200 ; intro line
    G92 E0 ; reset extruder
    G1 Z2.0 F3000 ; lower bed for clearance moving to print start

[gcode_macro Print_End]
gcode:
    M400                           ; wait for moves to finish
    M104 S0                        ; hotend off
    M107                           ; fans off
    G91                            ; relative positioning
    G1 E-1 F300                    ; retract the filament a bit before lifting the nozzle, to release some of the pressure
    G1 Z+20 E-5 X-20 Y-20 F3000    ; move Z up a bit and retract filament even more
    M117 Cooling please wait       ; progress indicator message
    G90                            ; absolute positioning
    G1 X130 Y20                    ; move to cooling position
    M190 R45                       ; set bed to cool off
    M84                            ; steppers off
    G90                            ; absolute positioning
    M117 Print complete            ; progress indicator message

################################################################################
# Telegram Messenging #
###############################################################################
[gcode_macro telegram_MSG]
gcode:
    RESPOND PREFIX=telegram: MSG="Test"

################################################################################
# Relay Control #
###############################################################################
[gcode_macro TOGGLE_PRINTER_POWER]
gcode:
  SET_PIN PIN=printer_power VALUE={(not printer['output_pin printer_power'].value)|int}

[gcode_macro TOGGLE_LIGHT]
gcode:
  SET_PIN PIN=light VALUE={(not printer['output_pin light'].value)|int}

################################################################################
# Homing Sensorless #
###############################################################################
[gcode_macro SENSORLESS_HOME_X]
gcode:
    INIT_TMC STEPPER=stepper_y
    INIT_TMC STEPPER=stepper_x
    INIT_TMC STEPPER=stepper_x
    {% set HOME_CUR = 0.800 %}
    {% set driver_config = printer.configfile.settings['tmc2209 stepper_x'] %}
    {% set RUN_CUR = driver_config.run_current %}
    {% set HOLD_CUR = driver_config.hold_current %}
    # Set current for sensorless homing
    SET_TMC_CURRENT STEPPER=stepper_x CURRENT={HOME_CUR} HOLDCURRENT={HOME_CUR}
    # Pause to ensure driver stall flag is clear
    G4 P2000
    # Home
    G28 X0
    # Move away
    G90
    G1 X5 F1200
    # Set current during print
    SET_TMC_CURRENT STEPPER=stepper_x CURRENT={RUN_CUR} HOLDCURRENT={HOME_CUR}

[gcode_macro SENSORLESS_HOME_Y]
gcode:
    {% set HOME_CUR = 0.800 %}
    {% set driver_config = printer.configfile.settings['tmc2209 stepper_y'] %}
    {% set RUN_CUR = driver_config.run_current %}
    {% set HOLD_CUR = driver_config.hold_current %}
    # Set current for sensorless homing
    SET_TMC_CURRENT STEPPER=stepper_y CURRENT={HOME_CUR} HOLDCURRENT={HOME_CUR}
    # Pause to ensure driver stall flag is clear
    G4 P2000
    # Home
    G28 Y0
    # Move away
    G90
    G1 Y5 F1200
    # Set current during print
    SET_TMC_CURRENT STEPPER=stepper_y CURRENT={RUN_CUR} HOLDCURRENT={HOLD_CUR}

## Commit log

2021-09-04 stl test, cleaning later
    [Gantry_Mount_Bracket_[L]_{b}.STL, Gantry_Mount_Bracket_[R]_{b}.STL, Gantry_Mount_[L]_{a}.STL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]
2021-09-15 Add v2.5, mirror changes, fix heat sets
    [corner_left v2.5.STL, corner_right v2.5.STL, xy_joiner_left_v2.5.STL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]
2021-09-16 Add joiner plates
    [xy_joiner_plate_mirror_v2.5.STL, xy_joiner_plate_v2.5.STL]
2021-09-16 Fixed folder structure
    [corner_left v2.5.STL, corner_right v2.5.STL, xy_joiner_left_v2.5.STL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]
2021-09-18 Update to 20T GT2 pulleys
    [Gantry_Mount_[L]_{a}.STL, Idler_Mount_[L]_{a}.STL]
2021-09-19 Remove versions, Update to 20T GT2 Pulleys
    [Gantry_Mount_Bracket_[L]_{b}.STL, Gantry_Mount_Bracket_[R]_{b}.STL, corner_left v2.5.STL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]
2021-11-21 Gantry clean up (#12)
    * Clean up Gantry Mount, add MGN12 supports
    * Delete Gantry_Mount_[L]_{b}_20t.STEP
    * Delete Gantry_Mount_Rail_Bracket[L]_{b}.STEP
    * Clean up Gantry_Mount, Add supports for MGN12
    * Clean up Gantry_Mount, Add supports for MGN12
    * Cleaned Gantry_Mount and test Rail_Bracket
    [Gantry_Mount_Rail_Bracket[L]_{b}.STEP, Gantry_Mount_Rail_Bracket[L]_{b}.STL, Gantry_Mount_[L]_{b}_20t.STEP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]
2022-01-06 Split into two Variants
    [Gantry_Mount_Bracket_[L]_{b}.STL, Gantry_Mount_Bracket_[R]_{b}.STL, Gantry_Mount_Rail_Bracket[L]_{b}.STEP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]
2022-01-06 GR9 Initial - not all parts yet
    [GR9_Gantry_Mount_Bracket_[R]_{b}.STL, GR9_Gantry_Mount_[L]_{b}_20t_v2.STL, GR9_Idler_Mount_[L]_{a}_20t_v2.STL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]
2022-01-31 Added X Extrusion section
2022-02-01 Add Klipper examples
    [GCODE_Macros (Sensorless).cfg, printer (Sensorless).cfg]
2022-02-01 Remove to prepare for v1
    [GR9_Gantry_Mount_Bracket_[R]_{b}.STL, GR9_Gantry_Mount_[L]_{b}_20t_v2.STL, GR9_Idler_Mount_[L]_{a}_20t_v2.STL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]
2022-02-01 Initial Release v1 STLs
    [GR9_Gantry_Bracket [Left] {a} v1 .stl, GR9_Gantry_Bracket [Right] {a} v1 .stl, GR9_Gantry_Mount [Left] {b} v1 .stl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]
2022-02-01 Fix incorrect Idler STL
    [GR9_Gantry_Bracket [Left] {a} v1 .stl, GR9_Gantry_Bracket [Right] {a} v1 .stl, GR9_Gantry_Mount [Left] {b} v1 .stl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]
2022-02-01 Incorrectly uploaded
    [GR9_Gantry_Bracket [Left] {a} v1 .stl, GR9_Gantry_Bracket [Right] {a} v1 .stl, GR9_Gantry_Mount [Left] {b} v1 .stl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]
2022-02-01 preparing for work flows
2022-02-02 Update main.yml
    Case-sensitive branch names issue
    now checks for only merges
2022-02-03 Add STEP, Add MGN mounting guides
    Add complete assembly in STEP. Add both MGN9 and MGN12 mounting guides for ease of assembly.
    Update Readme to reflect changes
    [GR9_MGN12_guide_block_2020_v1.stl, GR9_MGN9_guide_block_2020_v1.stl]
2022-02-05 Add rail lengths
2022-02-05 Remove version numbers
    [GR9_MGN12_guide_block_2020.stl, GR9_MGN9_guide_block_2020.stl]
2022-02-05 Add MGN12 Gantry Mount
    [GR9_MGN12_Gantry_Mount_TEST.STL]
2022-02-06 Add frame brace
    [GR9_Frame_Brace_TEST.stl]
2022-02-11 Fix MGN12 test mount spacing
    [GR9_MGN12_Gantry_Mount_TEST.STL, GR9_MGN12_Gantry_Mount_TEST_2.STEP]
2022-02-11 Add Stock Canopy Supports and GR Corners
    [GR9_CanopyMount_FrontLeft.stl, GR9_CanopyMount_RearLeft.stl, GR9_CanopyMount_Support.stl]
2022-02-21 Fix gantry belt pathing issue
    - Updated instructions for Pulley configs (to be verified)
    - New MGN mounting guides
    - New Frame braces for strengthening frame
    - Updated Gantry Bracket. Lots of minor changes to improve belt path and fixed a lot of annoying fillets.
    - New Canopy mounts for stock hood
    - New printed spacers (to be verified)
    - Added the BumpStop for the Left side Gantry Bracket
    - Added the MGN12 Gantry mount for crazy people who want to run MGN12 on Y
    [GR9_Canopy_Mount [FrontLeft] {a}.stl, GR9_Canopy_Mount [RearLeft] {a}.stl, GR9_Canopy_Support [Side] {a}.stl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]
2022-02-27 Repair the belt path
    - Fix gantry to remove pathing issue
    - Simplify printing of Gantry mount, remove un-needed fillets
    - Add spacers for both Stock and 20t pulleys
    - Make 20t pulleys a preferred option
    - Add pictures to readme
    - Fix errors in readme
    [13mm Spacer.stl, 14mm Spacer.stl, 15mm Spacer.stl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]
2022-03-01 Fix errors in Readme, fix Idler fillet
    [GR9_Idler [Left] {a} v1.stl, GR9_Idler [Right] {a} v1.stl]
2022-03-23 Replace incorrect STLs
    [GR9_Gantry_Mount [Left] {b}.stl, GR9_Gantry_Mount [Right] {b}.stl]
2022-03-30 Fix wrong STL (again...)
    [GR9_Gantry_Bracket [Left] {a} v1 .stl, GR9_Gantry_Bracket [Right] {a} v1 .stl]
